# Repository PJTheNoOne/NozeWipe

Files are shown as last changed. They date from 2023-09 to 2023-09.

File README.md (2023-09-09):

# Noze Wipe
A Voron nozzle wiper using silicone parts meant for the [Blackbox 3D Printer](https://layershift.xyz/blackbox3dprinter/). You can find these parts on [kb-3d](https://kb-3d.com/).

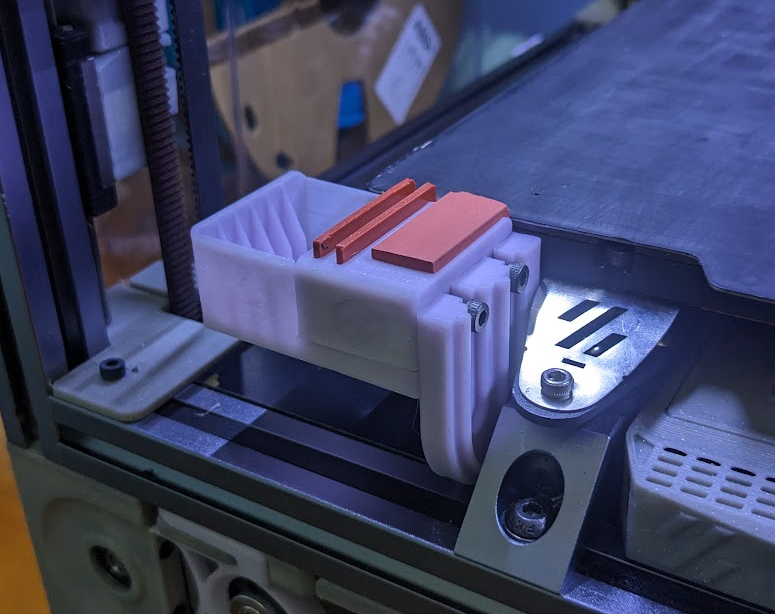
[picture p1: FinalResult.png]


The point of this mod is to provide a non-abrasive specifically designed nozzle wipe that is compatible with [Voron-Tap](https://github.com/VoronDesign/Voron-Tap), [Nevermore](https://github.com/nevermore3d/Nevermore_Micro), and the [Kinematic Bed](https://github.com/tanaes/whopping_Voron_mods/tree/main/kinematic_bed) mods.
## BOM
|Part|Amount|
|-|-|
|M3x8 SH|4|
|M3 T-nut|2|
|M3 Heatset-insert|2|
|6x3mm magnets|4|
|[Silicone Leak Blocker](https://kb-3d.com/store/cnc-laser-cut/22-silicone-leak-blocker-blackbox-1634506066001.html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)|1|
|[Silicone Nozzle Wiper](https://kb-3d.com/store/cnc-laser-cut/9-silicone-nozzle-wiper-blackbox-1634505999959.html)|2|
## Instantiation
### Physical
1. Print the parts using the [Voron printing settings](https://docs.vorondesign.com/sourcing.html#print-settings).
3. Carefully slip the [Silicone Nozzle Wiper](https://kb-3d.com/store/cnc-laser-cut/9-silicone-nozzle-wiper-blackbox-1634505999959.html) into the vertical slots on the holder.
4. Install heat-set inserts into the side of the holder.
5. Use hot glue or similar adhesive to affix the [Silicone Leak Blocker](https://kb-3d.com/store/cnc-laser-cut/22-silicone-leak-blocker-blackbox-1634506066001.html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).
6. If you want the bin, use hot glue or similar adhesive to affix magnets into the remaining holes.
7. Install t-nuts with holes closest together on the left outside bed rail.
8. Use 2 M3x8 SHs to install the mount.
9. Lightly screw the remaining M3x8 SHs into the holder and tighten when placed at the correct height on the mount. The top of the holder and bin should be level with the bed.
10. Done!
### Klipper

This is where it gets more complicated. There are several steps you will have to do.

1. Find the physical limits of your printer.
	- Allow Klipper to go past the extent of the bed.
2. Calibrate the locations of the wipe.
3. Testing.
4. Modify print_start.

#### Physical limits
To use this mod, the printer must travel past the normal limits of the bed. To do this, adjust the position_max and position_min in [stepper_x] and [stepper_y] sections of the printer.cfg.
You may also have to adjust the bed so that the nozzle can go past one side of the bed.

My config looks like this.

```ini
[stepper_x]
...
position_min: 0
position_max: 250
...

[stepper_x]
...
position_min: -7
position_max: 250
...
```
#### Installation
Copy and paste the NozeWipe.cfg file to your kilppers /config directory. Next, use [include NozeWipe.cfg] at the beginning of the printer.cfg file. Three locations must be defined; otherwise, you will get an error.

#### Calibration
```ASCII
                     ▐
                     ▐        BED
                     ▐
                     ▐
      y = 0╶╶╶╶╶╶╶╶╶╶▐▄▄▄▄▄▄▄▄▄▄▄▄▄▄▄▄▄▄▄▄▄▄▄▄▄▄▄▄▄▄▄▄▄▄▄▄
                     ╎    ╭──────────╮╭─┼─┼─╔═══╗╮
                     ╎    │╭────────╮││ ║ ║ ║   ║│
      all_y╶╶╶╶╶╶╶╶╶╶┼╶╶╶╶╶│╶╶╶╶╶╶╶╶│╶╶╶║╶║╶║╶╶╶║╶╶╶╶╶╶╶╶╶
                     ╎    ││ BIN    │││ ║ ║ ║   ║│<-HOLDER
                     x    ││      ∧ │││ ║ ║∧║ ∧ ║│
                     =    │╰──────┼─╯││ ║ ║╎╚═╎═╝│
                     0    ╰───────┼──╯╰────┼──┼──╯
     wipe_x╶╶╶╶╶╶╶╶╶╶╶╶╶╶╶╶╶╶╶╶╶╶╶┘        ╎  ╎
 wipe_end_x ╶╶╶╶╶╶╶╶╶╶╶╶╶╶╶╶╶╶╶╶╶╶╶╶╶╶╶╶╶╶╶┘  ╎
block_loc_x╶╶╶╶╶╶╶╶╶╶╶╶╶╶╶╶╶╶╶╶╶╶╶╶╶╶╶╶╶╶╶╶╶╶╶┘
```
The ASCII diagram above points to the locations that the nozzle will travel to. You must fill out six variables in the NozeWipe.cfg [gcode_macro POS] section. These are indicated by being set to 10000. Setting the values to 10000 allows the printer to start and move but not error out.

```INI
[gcode_macro POS]
variable_z_min_height: 10000
variable_z_lift_height: 10000
variable_all_y: 10000
variable_wipe_x: 10000
variable_wipe_end_x: 10000
variable_block_loc_x: 10000
...
```

##### Calibration Steps 
1. Home all.
2. Quad-Gantry-Level (QGL).
3. Go to (0,0,5).
4. Move y by 1mm to be past the bed and above the bin and holder when you find the correct location. Record the y value in the all_y variable.
5. Move x to be over the bin and record that value in wipe_x.
6. Move x between the wipes and the block and record the value in wipe_end_x.
7. Move x to be over the block and record the value as block_loc_x.
8. Move z down to be slightly pressing into the block. Record the value as z_min_height.
9. z_lift height should be around 10mm (in absolute coordinates). This value should clear all parts of the wiper.
10. Save and restart!

My resulting config looks like this:
```INI
[gcode_macro POS]
variable_z_min_height: 1.8
variable_z_lift_height: 5
variable_all_y: -7
variable_wipe_x: 0
variable_wipe_end_x: 17
variable_block_loc_x: 25
```
#### Testing
1. Ensure the printer does not crash while traveling to the new limits.
2. Home and QGL.
3. Use command \_Wipe_Home and check location.
4. Use command \_Wipe. The nozzle should wipe between the start and right before the block five times and lift after.
5. Use command \_Park_nozzle and check location. Adjust any of these values as needed using the ASCII diagram.
6. Save and restart!
#### Modify print_start

You will need a sequence that looks something like this:
1. Home.
2. Quad-Gantry-Level (QGL) or equivalent sequence.
3. ex. Heat bed and nozzle.
4. Use \_Wipe_Home (must be done before \_wipe)
5. Use \_wipe.
6. ex. park and cool to bed, safe temp.
7. Home with a clean nozzle.
8. ex. \_park_nozzle and heat.
9. Print!.

Note: The ex. sections are where you may want to do things differently than I did.

The following is what my print_start macro looks like.
```INI
[gcode_macro PRINT_START]
gcode:
G90 ; absolute positioning
CLEAN_NOZZLE EXTRUDER={params.EXTRUDER|float} BED={params.BED|float}
STATUS_HOMING
G28
{% set FILAMENT_TYPE = params.FILAMENT|default(PLA)|string %}
{% if FILAMENT_TYPE == "ABS" or FILAMENT_TYPE == "ASA" or FILAMENT_TYPE == "PET" %}
SET_FAN_SPEED FAN=Nevermore SPEED=0.8
{% endif %}
STATUS_HEATING
_PARK_NOZZLE
M104 T0 S{params.EXTRUDER|float}
M190 S{params.BED|float} ; Make sure bed is hot
M109 T0 S{params.EXTRUDER|float} ; Make sure hotend is hot
_WIPE_HOME
G92 E0
G1 E{20} ; Purge
G92 E0
_WIPE WIPE_COUNT=1
STATUS_PRINTING
```

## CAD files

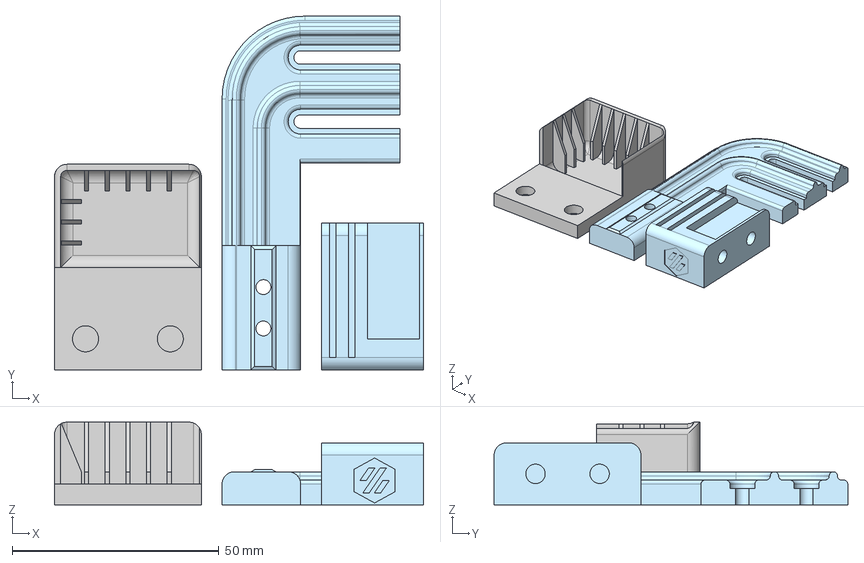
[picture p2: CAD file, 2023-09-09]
CADFiles/ReadyToPrint.step
89.2 x 85.5 x 20.0 mm
Holder
Bin
Mount

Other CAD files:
CADFiles/ReadyToPrint.x_t

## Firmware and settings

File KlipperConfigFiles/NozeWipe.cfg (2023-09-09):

[gcode_macro POS]
variable_z_min_height: 10000
variable_z_lift_height: 10000
variable_all_y: 10000
variable_wipe_x: 10000
variable_wipe_end_x: 10000
variable_block_loc_x: 10000
variable_wipe_count: 5
variable_retract_amount: -2
variable_feed: 3600
variable_extrude_feed: 120
variable_wipe_feed: 1200
variable_extrude_amount: 50
variable_retract_amount: -.75
gcode:
    M115

[gcode_macro clean_nozzle]
gcode:
    SAVE_GCODE_STATE NAME=clean_nozzle_state
    G90
    G32
    _WIPE_HOME
    STATUS_HEATING
    M140 S{params.BED|default(printer.heater_bed.target)|float}
    M109 T0 S{params.EXTRUDER|default(250)|float}
    M106 S255 ; Part fan to cool
    STATUS_CLEANING
    G1 E{params.E_AMOUNT|default(printer["gcode_macro POS"].extrude_amount)|float} F{printer["gcode_macro POS"].extrude_feed}; Purge
    G92 E0 
    G1 E{printer["gcode_macro POS"].retract_amount} F{printer["gcode_macro POS"].extrude_feed} ; Retract
    G92 E0
    _WIPE
    G1 E{printer["gcode_macro POS"].retract_amount} F{printer["gcode_macro POS"].extrude_feed} ; Retract
    G92 E0 
    _PARK_NOZZLE
    STATUS_COOLING
    M109 T0 S125 ; Decrease temp
    {% if params.COOL|default("False")|string == "TRUE"%}
      M104 T0 S0 ; Cool extruder
    {% endif %}
    M106 S0 ; Turn off fan
    _LIFT
    RESTORE_GCODE_STATE NAME=clean_nozzle_state

[gcode_macro _PARK_NOZZLE]
gcode:
    SAVE_GCODE_STATE NAME=_PARK_NOZZLE
    G90
    G0 Z{printer["gcode_macro POS"].z_lift_height}
    G0 X{printer["gcode_macro POS"].block_loc_x} Y{printer["gcode_macro POS"].all_y} Z{printer["gcode_macro POS"].z_lift_height} F{printer["gcode_macro POS"].feed}
    G0 Z{printer["gcode_macro POS"].z_min_height}
    RESTORE_GCODE_STATE NAME=_PARK_NOZZLE
[gcode_macro _WIPE]
gcode:
    SAVE_GCODE_STATE NAME=_WIPE
    G90
    {% set count = params.WIPE_COUNT|default(printer["gcode_macro POS"].wipe_count)|int %}
    {% for wipe in range(count) %}
      G0 X{printer["gcode_macro POS"].wipe_end_x} Y{printer["gcode_macro POS"].all_y} F{printer["gcode_macro POS"].wipe_feed}
      G0 X{printer["gcode_macro POS"].wipe_x} Y{printer["gcode_macro POS"].all_y} F{printer["gcode_macro POS"].wipe_feed}
    {% endfor %}
    G0 X{printer["gcode_macro POS"].wipe_end_x} Y{printer["gcode_macro POS"].all_y} F{printer["gcode_macro POS"].wipe_feed} ; Go to wipe end
    G0 Z{printer["gcode_macro POS"].z_lift_height} ; lift
    RESTORE_GCODE_STATE NAME=_WIPE
[gcode_macro _WIPE_HOME]
gcode:
    SAVE_GCODE_STATE NAME=_WIPE_HOME
    G90
    G0 Z{printer["gcode_macro POS"].z_lift_height} F{printer["gcode_macro POS"].feed}
    G0 X{printer["gcode_macro POS"].wipe_x} Y{printer["gcode_macro POS"].all_y} F{printer["gcode_macro POS"].feed}; Move to Wipe
    G0 Z{printer["gcode_macro POS"].z_min_height} F{printer["gcode_macro POS"].feed} ; Move Down
    RESTORE_GCODE_STATE NAME=_WIPE_HOME
[gcode_macro _LIFT]
gcode:
    SAVE_GCODE_STATE NAME=_LIFT
    G90
    G0 Z{printer["gcode_macro POS"].z_lift_height}
    RESTORE_GCODE_STATE NAME=_LIFT
